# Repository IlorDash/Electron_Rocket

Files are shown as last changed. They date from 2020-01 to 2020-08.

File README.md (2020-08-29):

# Electron_Rocket
Repository for Electron rocket project

Altimeter test - data from altimeter. In .txt files raw data from UART, in excel files altitude graphs. Altitude in centimeters  
BMP_280 Nucleo_L031K6 - code for altimeter  
Camera_Software - rocket-cam project (WIP)  
Model - 3D models of each detail  
Filter_xx - graphs of test of different noise filters  
Real-Rockets_RD1-20-5 - profile of Real Rockets engine for OpenRocket  
Rocket_project - OpenRocket file of my rocket configuration  
rocket_fly_test - data and graph of completed fly test

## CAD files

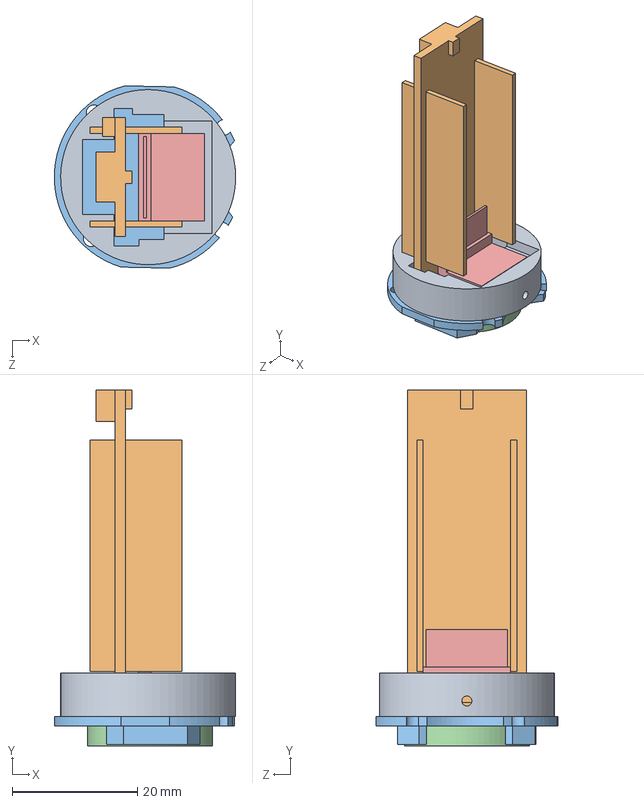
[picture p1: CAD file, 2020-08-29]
Models/Altimeter/Altimeter.SLDASM
29.0 x 56.9 x 29.2 mm
Altimeter_Mount
STM32L031K6
Battery_Mount
Battery_CR2032
BMP_280

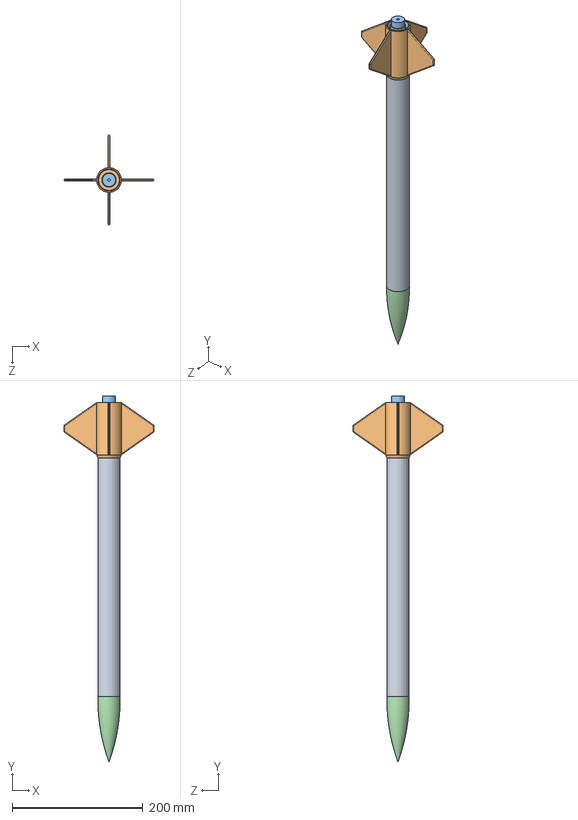
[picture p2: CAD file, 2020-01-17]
Models/Altimeter/Rocket_Assembly.SLDASM
137.9 x 560.0 x 137.9 mm
Body_Tube
Motor_Mount_RD-1-20-5
Motor_RD-1-20-5
Nose_Cone
Altimeter_Mount
STM32L031K6
Battery_Mount
Battery_CR2032
BMP_280
Fins_With_Mount
Parachute_and_rope

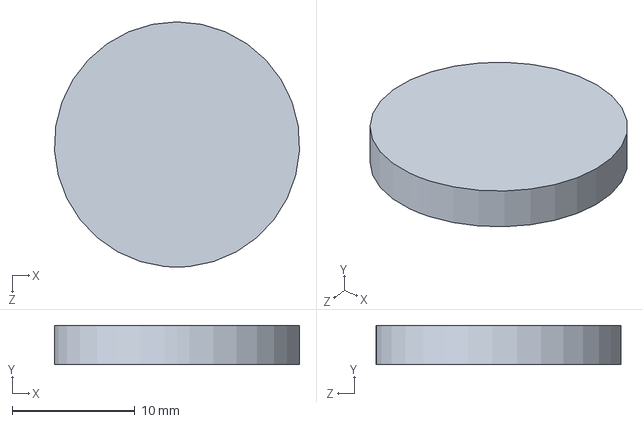
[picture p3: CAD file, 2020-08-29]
Models/Altimeter/Battery_CR2032.SLDPRT
20.0 x 3.20 x 20.0 mm

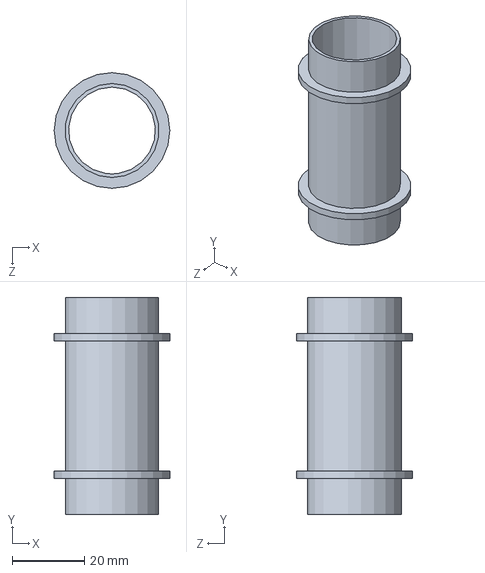
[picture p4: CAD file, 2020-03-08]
Models/Motors/Motor_Mount_RD-1-20(30)-5.SLDPRT
32.0 x 60.0 x 32.0 mm

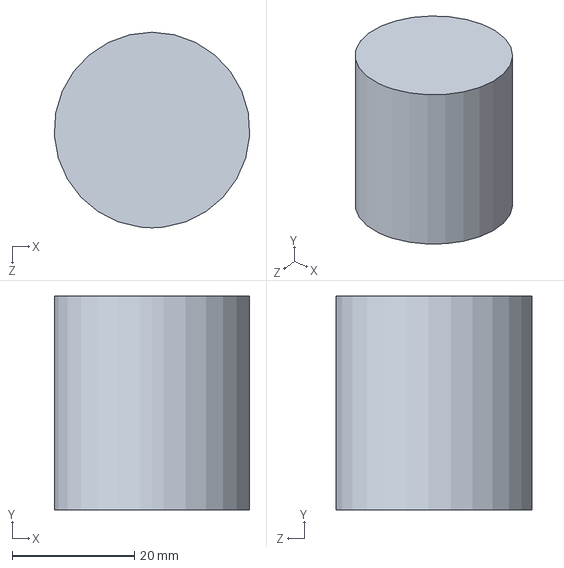
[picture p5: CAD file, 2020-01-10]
Models/Parachute_and_rope.SLDPRT
31.9 x 35.0 x 32.0 mm

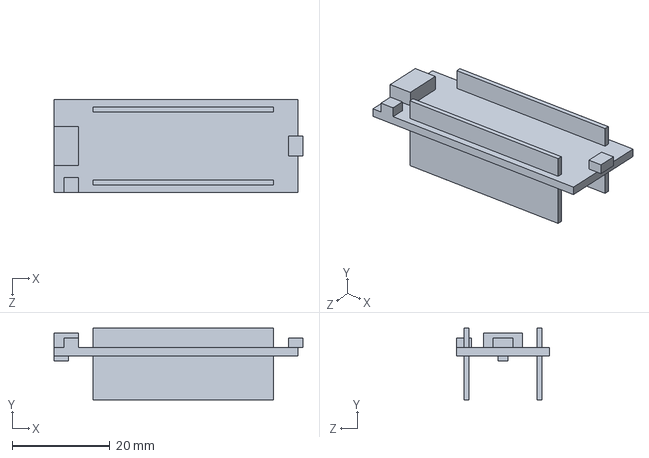
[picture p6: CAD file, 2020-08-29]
Models/Altimeter/STM32L031K6.SLDPRT
51.0 x 14.7 x 19.0 mm

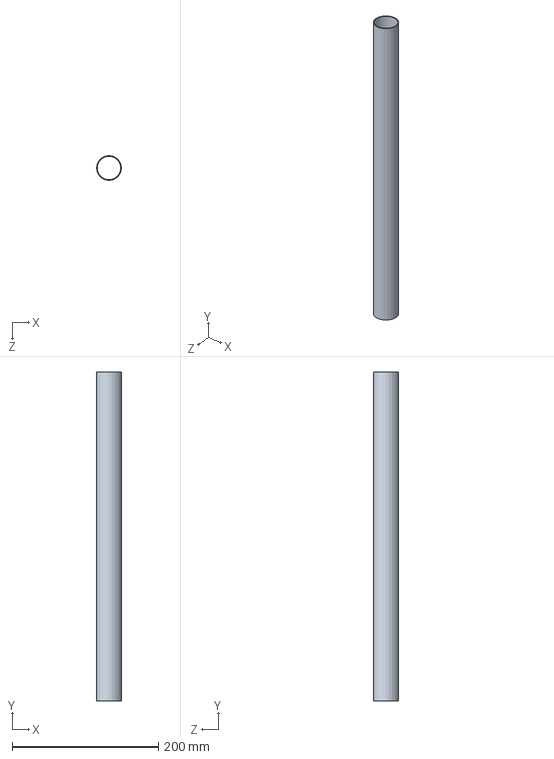
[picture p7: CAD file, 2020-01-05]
Models/Body_Tube.SLDPRT
34.0 x 450.0 x 34.0 mm

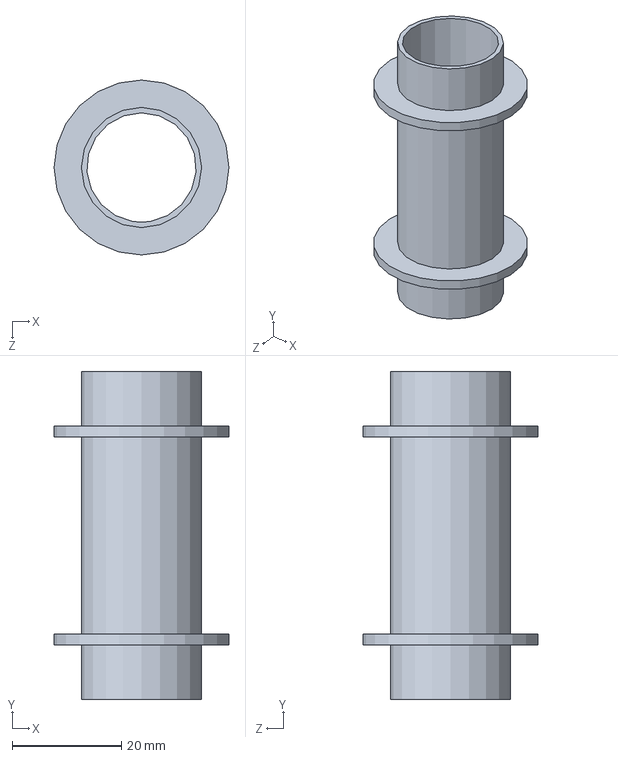
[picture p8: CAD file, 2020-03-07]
Models/Motors/Motor_Mount_RD-1-10-5.SLDPRT
32.0 x 60.0 x 32.0 mm

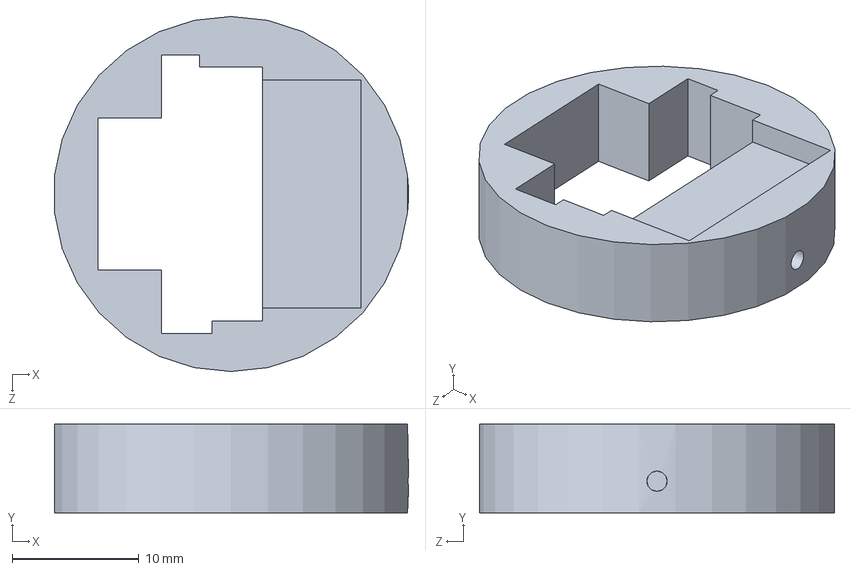
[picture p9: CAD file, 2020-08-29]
Models/Altimeter/Altimeter_Mount.SLDPRT
27.9 x 7.00 x 28.0 mm

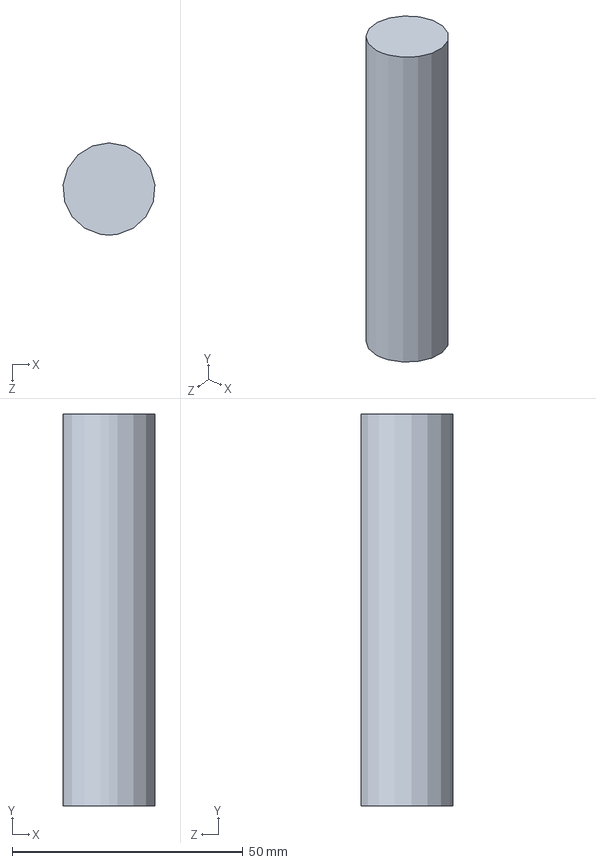
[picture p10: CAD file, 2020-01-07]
Models/Motors/Motor_RD-1-20-5.SLDPRT
19.9 x 85.0 x 20.0 mm

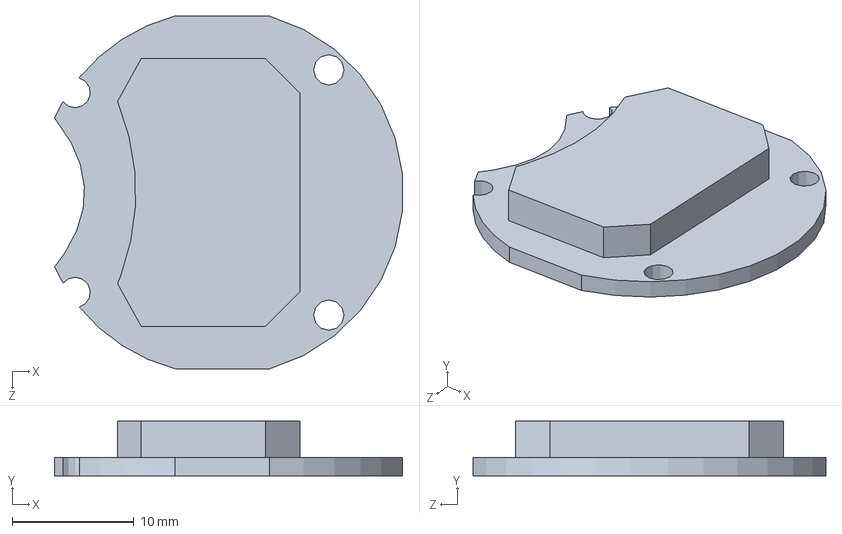
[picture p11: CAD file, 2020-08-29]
Models/Altimeter/Battery_Mount.SLDPRT
28.6 x 4.50 x 29.0 mm

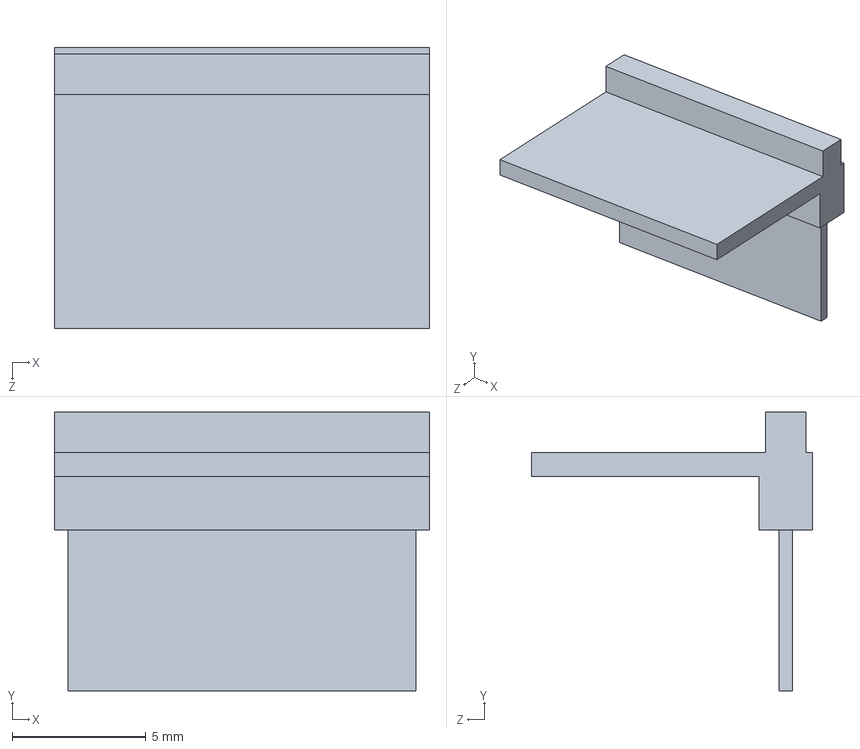
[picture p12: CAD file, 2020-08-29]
Models/Altimeter/BMP_280.SLDPRT
14.0 x 10.4 x 10.5 mm

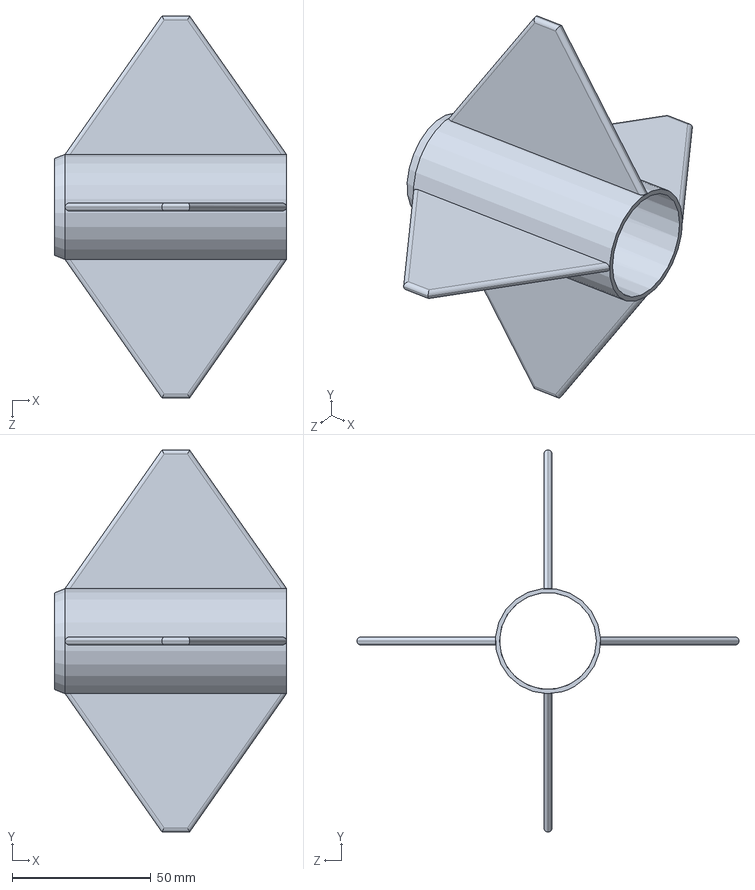
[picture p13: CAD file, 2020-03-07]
Models/Altimeter/Fins_With_Mount.SLDPRT
83.8 x 137.9 x 137.9 mm

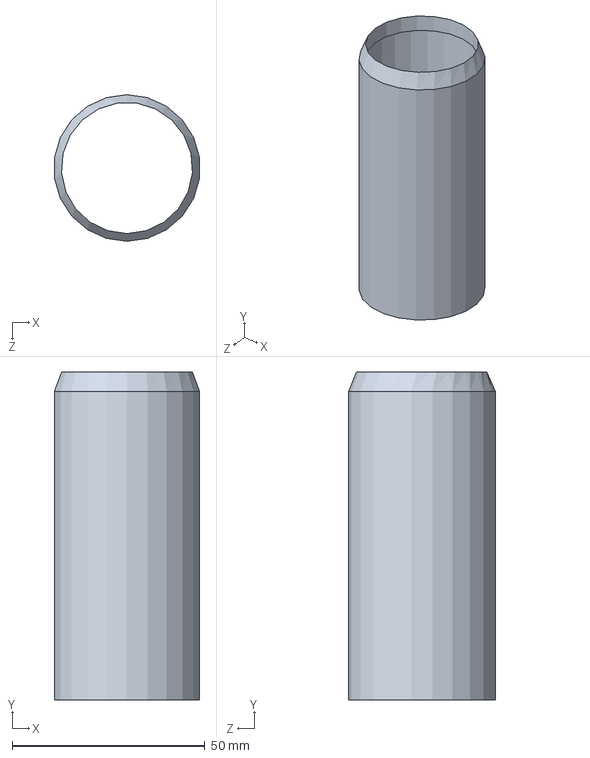
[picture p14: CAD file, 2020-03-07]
Models/Altimeter/Fins_Mount.SLDPRT
37.6 x 85.0 x 38.0 mm

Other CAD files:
Models/Altimeter/Nose_Cone.SLDPRT
Models/Altimeter/Fin.SLDPRT

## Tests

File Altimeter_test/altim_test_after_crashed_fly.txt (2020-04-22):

0	-4
1	-3
2	-2
3	0
4	0
5	2
6	5
7	8
8	8
9	11
10	15
11	17
12	17
13	18
14	20
15	18
16	18
17	17
18	17
19	15
20	15
21	12
22	10
23	9
24	10
25	10
26	10
27	11
28	11
29	13
30	16
31	12
32	14
33	12
34	14
35	16
36	14
37	14
38	14
39	17
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

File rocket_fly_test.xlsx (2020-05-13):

0 | 3 | в метраз | 0.03
1 | 0 |  | 0 | 148.19
2 | 0 |  | 0
3 | 0 |  | 0
4 | 0 |  | 0
5 | 3 |  | 0.03
6 | 2 |  | 0.02
7 | 2 |  | 0.02
8 | 2 |  | 0.02
9 | 2 |  | 0.02
10 | 2 |  | 0.02
11 | 2 |  | 0.02
12 | 5 |  | 0.05
13 | 5 |  | 0.05
14 | 5 |  | 0.05
15 | 4 |  | 0.04
16 | 2 |  | 0.02
17 | 2 |  | 0.02
18 | 2 |  | 0.02
19 | 2 |  | 0.02
20 | 1 |  | 0.01
21 | 1 |  | 0.01
22 | 0 |  | 0
23 | 3 |  | 0.03
24 | 1 |  | 0.01
25 | 1 |  | 0.01
26 | 1 |  | 0.01
27 | 3 |  | 0.03
28 | 3 |  | 0.03
29 | 3 |  | 0.03
30 | 8 |  | 0.08
31 | 8 |  | 0.08
32 | 8 |  | 0.08
33 | 8 |  | 0.08
34 | 8 |  | 0.08
35 | 8 |  | 0.08
36 | 6 |  | 0.06
37 | 6 |  | 0.06
38 | 6 |  | 0.06
39 | 8 |  | 0.08
40 | 6 |  | 0.06
41 | 4 |  | 0.04
42 | 4 |  | 0.04
43 | 4 |  | 0.04
44 | 6 |  | 0.06
45 | 4 |  | 0.04
46 | 8 |  | 0.08
47 | 8 |  | 0.08
48 | 8 |  | 0.08
49 | 9 |  | 0.09
50 | 9 |  | 0.09
51 | 9 |  | 0.09
52 | 9 |  | 0.09
53 | 12 |  | 0.12
54 | 10 |  | 0.1
55 | 10 |  | 0.1
56 | 10 |  | 0.1
57 | 12 |  | 0.12
58 | 12 |  | 0.12
59 | 12 |  | 0.12
60 | 17 |  | 0.17
61 | 17 |  | 0.17
62 | 17 |  | 0.17
63 | 15 |  | 0.15
64 | 15 |  | 0.15
65 | 15 |  | 0.15
66 | 15 |  | 0.15
67 | 15 |  | 0.15
68 | 17 |  | 0.17
69 | 17 |  | 0.17
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

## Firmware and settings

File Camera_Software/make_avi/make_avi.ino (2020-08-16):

/*

  TimeLapseAvi

  ESP32-CAM Video Recorder

  This program records an AVI video on the SD Card of an ESP32-CAM.
  
  by James Zahary July 20, 2019
     jamzah.plc@gmail.com

  https://github.com/jameszah/ESP32-CAM-Video-Recorder
    jameszah/ESP32-CAM-Video-Recorder is licensed under the
    GNU General Public License v3.0

  Acknowlegements:

  1.  https://robotzero.one/time-lapse-esp32-cameras/
      Timelapse programs for ESP32-CAM version that sends snapshots of screen.
  2.  https://github.com/nailbuster/esp8266FTPServer
      ftp server (slightly modifed to get the directory function working)
  3.  https://github.com/ArduCAM/Arduino/tree/master/ArduCAM/examples/mini
      ArduCAM Mini demo (C)2017 LeeWeb: http://www.ArduCAM.com
      I copied the structure of the avi file, some calculations.

  The is Arduino code, with standard setup for ESP32-CAM
    - Board ESP32 Wrover Module
    - Partition Scheme Huge APP (3MB No OTA)
    
  This program records an AVI video on the SD Card of an ESP32-CAM.
  
  It will record realtime video at limited framerates, or timelapses with the full resolution of the ESP32-CAM.
  It is controlled by a web page it serves to stop and start recordings with many parameters, and look through the viewfinder.
  
  You can control framesize (UXGA, VGA, ...), quality, length, and fps to record, and fps to playback later, etc.

  framesize can be UXGA, SVGA, VGA, CIF (default VGA)
  length is length in seconds of the recording 0..3600 (default 1800)
  interval is the milli-seconds between frames (default 200)
  quality is a number 5..50 for the jpeg  - smaller number is higher quality with bigger and more detailed jpeg (default 10)
  repeat is a number of who many of the same recordings should be made (default 100)
  speed is a factor to speed up realtime for a timelapse recording - 1 is realtime (default 1)
  gray is 1 for a grayscale video (default 0 - color)

  These factors have to be within the limit of the SD chip to receive the data.
  For example, using a LEXAR 300x 32GB microSDHC UHS-I, the following works for me:

  UXGA quality 10,  2 fps (or interval of 500ms)
  SVGA quality 10,  5 fps (200ms)
  VGA  quality 10, 10 fps (100ms)
  CIG  quality 10, 20 fps (50ms)

  If you increase fps, you might have to reduce quality or framesize to keep it from dropping frames as it writes all the data to the SD chip.

  Also, other SD chips will be faster or slower.  I was using a SanDisk 16GB microSDHC "Up to 653X" - which was slower and more unpredictable than the LEXAR ???

  Search for "zzz" to find places to modify the code for:
    1.  Your wifi name and password
    2.  Your preferred ip address (with default gateway, etc)
    3.  Your Timezone for use in filenames
    4.  Defaults for framesize, quality, ... and if the recording should start on reboot of the ESP32 without receiving a command
  
*/



#include "esp_camera.h"

// MicroSD
#include "driver/sdmmc_host.h"
#include "driver/sdmmc_defs.h"
#include "sdmmc_cmd.h"
#include "SD_MMC.h"
#include "esp_vfs_fat.h"

//nrf24
#include  <SPI.h>
#include "nRF24L01.h"
#include "RF24.h"

//vars for nrf24
char msg[6] = "hello";
bool radioNeedSetup = true;
RF24 radio(2, 15, 14, 12, 13);
const uint64_t _pipe = 0xE8E8F0F0E1LL;

void radioSetup(){
  radio.begin();
  radio.setChannel(120);
  radio.setPayloadSize(7);
  radio.openWritingPipe(_pipe);
  radio.setDataRate(RF24_250KBPS);
  radio.setPALevel(RF24_PA_MAX);
  radio.powerUp(); //начать работу
  radio.stopListening();  //не слушаем радиоэфир, мы передатчик
  radio.printDetails(); 
}

// my variables
#define LED_PIN 3
#define BUTTON_PIN 13

unsigned long lastFlash = 0;
bool record = false;

long current_millis;
long last_capture_millis = 0;
static esp_err_t cam_err;
static esp_err_t card_err;
char strftime_buf[64];
int file_number = 0;
bool internet_connected = false;
struct tm timeinfo;
time_t now;

char *filename ;
char *stream ;
int newfile = 0;
int frames_so_far = 0;
FILE *myfile;
long bp;
long ap;
long bw;
long aw;
long totalp;
long totalw;
float avgp;
float avgw;
int overtime_count = 0;

// CAMERA_MODEL_AI_THINKER
#define PWDN_GPIO_NUM     32
#define RESET_GPIO_NUM    -1
#define XCLK_GPIO_NUM      0
#define SIOD_GPIO_NUM     26
#define SIOC_GPIO_NUM     27
#define Y9_GPIO_NUM       35
#define Y8_GPIO_NUM       34
#define Y7_GPIO_NUM       39
#define Y6_GPIO_NUM       36
#define Y5_GPIO_NUM       21
#define Y4_GPIO_NUM       19
#define Y3_GPIO_NUM       18
#define Y2_GPIO_NUM        5
#define VSYNC_GPIO_NUM    25
#define HREF_GPIO_NUM     23
#define PCLK_GPIO_NUM     22


// GLOBALS
#define BUFFSIZE 512



// these are just declarations -- look below to edit defaults 

int capture_interval = 200; // microseconds between captures
int total_frames = 300;     // default updated below
int recording = 1;          // default start recording on reboot
int framesize = 6;          // vga
int repeat = 100;           // capture 100 videos
int quality = 10;
int xspeed = 1;
int xlength = 3;
int gray = 0;

int delay_between_captures = 0;

#define AVIOFFSET 240 // AVI main header length

unsigned long movi_size = 0;
unsigned long jpeg_size = 0;
unsigned long idx_offset = 0;

uint8_t zero_buf[4] = {0x00, 0x00, 0x00, 0x00};
uint8_t   dc_buf[4] = {0x30, 0x30, 0x64, 0x63};    // "00dc"
uint8_t avi1_buf[4] = {0x41, 0x56, 0x49, 0x31};    // "AVI1"
uint8_t idx1_buf[4] = {0x69, 0x64, 0x78, 0x31};    // "idx1"

uint8_t  vga_w[2] = {0x80, 0x02}; // 640
uint8_t  vga_h[2] = {0xE0, 0x01}; // 480
uint8_t  cif_w[2] = {0x90, 0x01}; // 400
uint8_t  cif_h[2] = {0x28, 0x01}; // 296
uint8_t svga_w[2] = {0x20, 0x03}; //
uint8_t svga_h[2] = {0x58, 0x02}; //
uint8_t uxga_w[2] = {0x40, 0x06}; // 1600
uint8_t uxga_h[2] = {0xB0, 0x04}; // 1200


const int avi_header[AVIOFFSET] PROGMEM = {
  0x52, 0x49, 0x46, 0x46, 0xD8, 0x01, 0x0E, 0x00, 0x41, 0x56, 0x49, 0x20, 0x4C, 0x49, 0x53, 0x54,
  0xD0, 0x00, 0x00, 0x00, 0x68, 0x64, 0x72, 0x6C, 0x61, 0x76, 0x69, 0x68, 0x38, 0x00, 0x00, 0x00,
  0xA0, 0x86, 0x01, 0x00, 0x80, 0x66, 0x01, 0x00, 0x00, 0x00, 0x00, 0x00, 0x10, 0x00, 0x00, 0x00,
  0x64, 0x00, 0x00, 0x00, 0x00, 0x00, 0x00, 0x00, 0x01, 0x00, 0x00, 0x00, 0x00, 0x00, 0x00, 0x00,
  0x80, 0x02, 0x00, 0x00, 0xe0, 0x01, 0x00, 0x00, 0x00, 0x00, 0x00, 0x00, 0x00, 0x00, 0x00, 0x00,
  0x00, 0x00, 0x00, 0x00, 0x00, 0x00, 0x00, 0x00, 0x4C, 0x49, 0x53, 0x54, 0x84, 0x00, 0x00, 0x00,
  0x73, 0x74, 0x72, 0x6C, 0x73, 0x74, 0x72, 0x68, 0x30, 0x00, 0x00, 0x00, 0x76, 0x69, 0x64, 0x73,
  0x4D, 0x4A, 0x50, 0x47, 0x00, 0x00, 0x00, 0x00, 0x00, 0x00, 0x00, 0x00, 0x00, 0x00, 0x00, 0x00,
  0x01, 0x00, 0x00, 0x00, 0x01, 0x00, 0x00, 0x00, 0x00, 0x00, 0x00, 0x00, 0x0A, 0x00, 0x00, 0x00,
  0x00, 0x00, 0x00, 0x00, 0x00, 0x00, 0x00, 0x00, 0x00, 0x00, 0x00, 0x00, 0x73, 0x74, 0x72, 0x66,
  0x28, 0x00, 0x00, 0x00, 0x28, 0x00, 0x00, 0x00, 0x80, 0x02, 0x00, 0x00, 0xe0, 0x01, 0x00, 0x00,
  0x01, 0x00, 0x18, 0x00, 0x4D, 0x4A, 0x50, 0x47, 0x00, 0x84, 0x03, 0x00, 0x00, 0x00, 0x00, 0x00,
  0x00, 0x00, 0x00, 0x00, 0x00, 0x00, 0x00, 0x00, 0x00, 0x00, 0x00, 0x00, 0x49, 0x4E, 0x46, 0x4F,
  0x10, 0x00, 0x00, 0x00, 0x6A, 0x61, 0x6D, 0x65, 0x73, 0x7A, 0x61, 0x68, 0x61, 0x72, 0x79, 0x67,
  0x6D, 0x61, 0x69, 0x6C, 0x4C, 0x49, 0x53, 0x54, 0x00, 0x01, 0x0E, 0x00, 0x6D, 0x6F, 0x76, 0x69,
};


//
// Writes an uint32_t in Big Endian at current file position
//
static void inline print_quartet(unsigned long i, FILE * fd)
{
  uint8_t x[1];

  x[0] = i % 0x100;
  size_t i1_err = fwrite(x , 1, 1, fd);
  i = i >> 8;  x[0] = i % 0x100;
  size_t i2_err = fwrite(x , 1, 1, fd);
  i = i >> 8;  x[0] = i % 0x100;
  size_t i3_err = fwrite(x , 1, 1, fd);
  i = i >> 8;  x[0] = i % 0x100;
  size_t i4_err = fwrite(x , 1, 1, fd);
}

char the_page[3000];

#include "soc/soc.h"
#include "soc/rtc_cntl_reg.h"


void setup() {


  Serial.begin(115200);

  Serial.setDebugOutput(true);
  


  pinMode(33, OUTPUT);    // little red led on back of chip
  //pinMode (LED_BUILTIN, OUTPUT); // flash light
  pinMode(LED_PIN, OUTPUT);
  pinMode(BUTTON_PIN, INPUT);

  digitalWrite(33, LOW);           // turn on the red LED on the back of chip

  camera_config_t config;
  config.ledc_channel = LEDC_CHANNEL_0;
  config.ledc_timer = LEDC_TIMER_0;
  config.pin_d0 = Y2_GPIO_NUM;
  config.pin_d1 = Y3_GPIO_NUM;
  config.pin_d2 = Y4_GPIO_NUM;
  config.pin_d3 = Y5_GPIO_NUM;
  config.pin_d4 = Y6_GPIO_NUM;
  config.pin_d5 = Y7_GPIO_NUM;
  config.pin_d6 = Y8_GPIO_NUM;
  config.pin_d7 = Y9_GPIO_NUM;
  config.pin_xclk = XCLK_GPIO_NUM;
  config.pin_pclk = PCLK_GPIO_NUM;
  config.pin_vsync = VSYNC_GPIO_NUM;
  config.pin_href = HREF_GPIO_NUM;
  config.pin_sscb_sda = SIOD_GPIO_NUM;
  config.pin_sscb_scl = SIOC_GPIO_NUM;
  config.pin_pwdn = PWDN_GPIO_NUM;
  config.pin_reset = RESET_GPIO_NUM;
  config.xclk_freq_hz = 20000000;
  config.pixel_format = PIXFORMAT_JPEG;

  //init with high specs to pre-allocate larger buffers
  if (psramFound()) {
    config.frame_size = FRAMESIZE_UXGA;
    config.jpeg_quality = 1;
    config.fb_count = 2;
  } else {
    config.frame_size = FRAMESIZE_SVGA;         // svga 12 fails due to jpg 60000
    config.jpeg_quality = 12;
    config.fb_count = 1;
  }

  // camera init
  
  cam_err = esp_camera_init(&config);
  if (cam_err != ESP_OK) {
    Serial.printf("Camera init failed with error 0x%x", cam_err);
    major_fail();
    return;
  }

  // SD camera init
  card_err = init_sdcard();
  SD_MMC.begin("/sdcard", true);
  if (card_err != ESP_OK) {
    Serial.printf("SD Card init failed with error 0x%x", card_err);
    major_fail();
    return;
  }

  // 200 ms x 150 frames = 30 seconds     is 3 MB indoors
  // 200 ms x 300 frames = 1 minute       is about 6MD indoor
  // 20 ms x 3000 frames = 10 minute      is 60 MB indoor
  // burst 1000 frames gives 8 fps rather than 5, so 2 minutues 20 MB indoor

  digitalWrite(33, HIGH);


  //
  //  startup defaults  -- EDIT HERE 
  //  zzz

  sensor_t * s = esp_camera_sensor_get();
  s->set_framesize(s, FRAMESIZE_VGA);
  s->set_quality(s, 10);
  do_fb();                  // do a couple captures to make sure camera has new config
  do_fb();

  framesize = 6;            // vga
  repeat = 0;             // video + 1
  xspeed = 1;               // playback at 1 x realtime
  gray = 0;                 // not gray

  quality = 50;             // quality 10 - pretty good.  Goes from 0..63, but 0-5 sometimes fails on bright scenery (jpg too big for ESP32CAM system)
  capture_interval = 2;   //  milli-secconds per frame
  delay_between_captures = 45;

  total_frames = 100;       // total_frames x capture_interval = record_timea
  
  xlength = total_frames * (capture_interval + delay_between_captures); // in ms

  newfile = 0;    // no file is open  // don't fiddle with this!
  recording = 1;  // start recording on reboot without sending a command

}

//
// if we have no camera, or sd card, then flash rear led on and off to warn the human SOS - SOS
//
void major_fail() {
  while (1) {
    digitalWrite(33, LOW);
    delay(100);
    digitalWrite(33, HIGH);
    delay(100);

    digitalWrite(33, LOW);
    delay(100);
    digitalWrite(33, HIGH);
    delay(100);

    digitalWrite(33, LOW);
    delay(100);
    digitalWrite(33, HIGH);
    //delay(100);

    delay(1000);

    digitalWrite(33, LOW);
    delay(500);
    digitalWrite(33, HIGH);
    delay(500);

    digitalWrite(33, LOW);
    delay(500);
    digitalWrite(33, HIGH);
    delay(500);

    digitalWrite(33, LOW);
    delay(500);
    digitalWrite(33, HIGH);
    //delay(500);

    delay(1000);
  }
}

static esp_err_t init_sdcard()
{

  esp_err_t ret = ESP_FAIL;
  sdmmc_host_t host = SDMMC_HOST_DEFAULT();
  sdmmc_slot_config_t slot_config = SDMMC_SLOT_CONFIG_DEFAULT();
  esp_vfs_fat_sdmmc_mount_config_t mount_config = {
    .format_if_mount_failed = false,
    .max_files = 10,
  };
  sdmmc_card_t *card;

  Serial.println("Mounting SD card...");
  ret = esp_vfs_fat_sdmmc_mount("/sdcard", &host, &slot_config, &mount_config, &card);

  if (ret == ESP_OK) {
    Serial.println("SD card mount successfully!");
  }  else  {
    Serial.printf("Failed to mount SD card VFAT filesystem. Error: %s", esp_err_to_name(ret));
    major_fail();
  }

  Serial.print("SD_MMC Begin: "); Serial.println(SD_MMC.begin());   // required by ftp system ??
}

//////////////////////////////////////////////////////////////
// save photo stuff not currently used

static esp_err_t save_photo_numbered()
{
  file_number++;
  Serial.print("Taking picture: ");
  Serial.print(file_number);
  camera_fb_t *fb = esp_camera_fb_get();

  char *filename = (char*)malloc(21 + sizeof(int));
  sprintf(filename, "/sdcard/capture_%d.jpg", file_number);

  Serial.println(filename);
  FILE *file = fopen(filename, "w");
  if (file != NULL)  {
    size_t err = fwrite(fb->buf, 1, fb->len, file);
    Serial.printf("File saved: %s\n", filename);
  }  else  {
    Serial.println("Could not open file");
  }
  fclose(file);
  esp_camera_fb_return(fb);
  free(filename);
}



static esp_err_t save_photo_dated()
{
  Serial.println("Taking a picture...");
  camera_fb_t *fb = esp_camera_fb_get();

  time(&now);
  localtime_r(&now, &timeinfo);
  strftime(strftime_buf, sizeof(strftime_buf), "%F__%H%M%S", &timeinfo);

  char fname[100];

  if (framesize == 6) {
    sprintf(fname, "/sdcard/%s_vga_%d.jpg", strftime_buf, quality);
  } else if (framesize == 7) {
    sprintf(fname, "/sdcard/%s_svga_%d.jpg", strftime_buf, quality);
  } else if (framesize == 10) {
    sprintf(fname, "/sdcard/%s_uxga_%d.jpg", strftime_buf, quality);
  } else  if (framesize == 5) {
    sprintf(fname, "/sdcard/%s_cif_%d.jpg", strftime_buf, quality);
  } else {
    Serial.println("Wrong framesize");
    sprintf(fname, "/sdcard/%s_xxx_%d.jpg", strftime_buf, quality);
  }

  FILE *file = fopen(fname, "w");
  if (file != NULL)  {
    size_t err = fwrite(fb->buf, 1, fb->len, file);
    Serial.printf("File saved: %s\n", fname);

  }  else  {
    Serial.println("Could not open file");
  }
  fclose(file);
  esp_camera_fb_return(fb);

}

void save_photo()
{
  if (timeinfo.tm_year < (2016 - 1900) || internet_connected == false) { // if no internet or time not set
    save_photo_numbered(); // filenames in numbered order
  } else {
    save_photo_dated(); // filenames with date and time
  }
}



//~~~~~~~~~~~~~~~~~~~~~~~~~~~~~~~~~~~~~~~~~~~~~~~~~~~~~~~~~~~~~~~~~~~~~~~~~~~~~~~~~
//
// Make the avi move in 4 pieces
//
// make_avi() called in every loop, which calls below, depending on conditions
//   start_avi() - open the file and write headers
//   another_pic_avi() - write one more frame of movie
//   end_avi() - write the final parameters and close the file

// global variable used by these pieces

char str[20];
uint16_t n;
uint8_t buf[BUFFSIZE];

static int i = 0;
uint8_t temp = 0, temp_last = 0;
unsigned long fileposition = 0;
uint16_t frame_cnt = 0;
uint16_t remnant = 0;
uint32_t length = 0;
uint32_t startms;
uint32_t elapsedms;
uint32_t uVideoLen = 0;
bool is_header = false;
long bigdelta = 0;

camera_fb_t * fb = NULL;

FILE *avifile = NULL;
FILE *idxfile = NULL;

void make_avi( ) {

  // we are recording, but no file is open

  if (newfile == 0 && recording == 1) {                                     // open the file

    //save_photo_dated();

    start_avi();

    digitalWrite(33, HIGH);
    newfile = 1;
    totalp = 0;
    totalw = 0;
    frame_cnt = 0;
    frames_so_far = 0;

  } else {

    // we have a file open, but not recording

    if (newfile == 1 && recording == 0) {                                  // got command to close file
      digitalWrite(33, LOW);

      end_avi();

      Serial.println("Done capture due to command");

      frames_so_far = total_frames;

      newfile = 0;    // file is closed
      recording = 0;  // DO NOT start another recording

    } else {

      if (newfile == 1 && recording == 1) {                            // regular recording

        if (frames_so_far == total_frames)  {                                // we are done the recording

          Serial.println("Done capture for total frames!");

          digitalWrite(33, LOW);                                                       // close the file
          end_avi();

          frames_so_far = 0;
          newfile = 0;          // file is closed

          if (repeat > 0) {
            recording = 1;        // start another recording
            repeat = repeat - 1;
          } else {
            recording = 0;
          }
          
        } else if ((millis() - startms) > xlength) {

          Serial.println (" "); Serial.println("Done capture for time");
          Serial.print("Time Elapsed: "); Serial.print(millis() - startms); Serial.print(" Frames: "); Serial.println(frame_cnt);
          Serial.print("Config:       "); Serial.print(total_frames * capture_interval ) ; Serial.print(" (");
          Serial.print(total_frames); Serial.print(" x "); Serial.print(capture_interval);  Serial.println(")");

          digitalWrite(33, LOW);                                                       // close the file

          end_avi();

          frames_so_far = 0;
          newfile = 0;          // file is closed
          if (repeat > 0) {
            recording = 1;        // start another recording
            repeat = repeat - 1;
          } else {
            recording = 0;
          }

        } else  {                                                            // regular

          /*current_millis = millis();

          if (current_millis - last_capture_millis > capture_interval) {   */                    // Take another picture - fixed interval

            //if ((current_millis - startms) > (frame_cnt * capture_interval)) {                   // Take another picture - with catch up

            //last_capture_millis = millis();

            frames_so_far = frames_so_far + 1;
            frame_cnt++;

            another_pic_avi();
            
          //}
        }
      }
    }
  }
}
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
void loop()
{
  if (((digitalRead(BUTTON_PIN) == HIGH) || (record == true)) && (recording == 1))
    {
        if ((millis() - time_after_last_capture) >= delay_between_captures)             //make_avi check
        {
          make_avi();
          time_after_last_capture = millis();
        }
        
        
        record = true;
        
        if (millis() - lastFlash >= 1000)
        {
          lastFlash = millis();
          digitalWrite(LED_PIN, HIGH); //flash light
        } else if(millis() - lastFlash >= 1000)
        {
          digitalWrite(LED_PIN, LOW); //off light
          lastFlash = millis();
        }       
    }
    if(recording == 0){
      if(radioNeedSetup){
        radioSetup();
        radioNeedSetup = false;
      }
      Serial.print("Sending ");
      Serial.println(msg);
      radio.write(msg, 6);
      delay(10);
    }
    
}

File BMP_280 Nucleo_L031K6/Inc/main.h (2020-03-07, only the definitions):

#define TMS_Pin GPIO_PIN_13
#define TMS_GPIO_Port GPIOA
#define TCK_Pin GPIO_PIN_14
#define TCK_GPIO_Port GPIOA
#define LD3_Pin GPIO_PIN_3
#define LD3_GPIO_Port GPIOB
#define VCP_TX_Pin GPIO_PIN_6
#define VCP_TX_GPIO_Port GPIOB
#define VCP_RX_Pin GPIO_PIN_7
#define VCP_RX_GPIO_Port GPIOB

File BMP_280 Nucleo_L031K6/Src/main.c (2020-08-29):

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

/* Includes ------------------------------------------------------------------*/
#include "main.h"

/* USER CODE BEGIN Includes */
#include "bmp280.h"
/* USER CODE END Includes */

/* USER CODE BEGIN PTD */
#define MEASURMENTS_NUM 50
#define NUM_OF_FLASH_CELLS 4096
#include <string.h>
#include <stdio.h>
/* USER CODE END PTD */

I2C_HandleTypeDef hi2c1;

UART_HandleTypeDef huart2;

BMP280_HandleTypedef bmp280;

/* USER CODE BEGIN PV */
float pressure, temperature, humidity;

uint32_t data_to_flash;
uint8_t data_to_uart[128];
uint16_t size_to_uart;
float altitude_0 = 0;
float altitude_above_ground = 0;
float altitude_above_ground_prev = 0;
float altitude_t = 0;
float altitude_current = 0;
float altitude_to_flash = 0;
uint8_t flash_step = 4; // 4 bytes for measurment

char *status = "";
/* USER CODE END PV */

void SystemClock_Config(void);
static void MX_GPIO_Init(void);
static void MX_USART2_UART_Init(void);
static void MX_I2C1_Init(void);
/* USER CODE BEGIN PFP */

bool SaveFlashData(uint32_t dest, uint32_t *pSrc, uint16_t size) {
	while (HAL_FLASH_Unlock() != HAL_OK) {
	}

	uint32_t *pDest = (uint32_t *)dest;
	uint32_t *pDestEnd = pDest + size;
	uint32_t pageToBeErase = (uint32_t)pDest & ~(FLASH_PAGE_SIZE - 1);
	while (pDest < pDestEnd) {
		if (FLASH_WaitForLastOperation(FLASH_TIMEOUT_VALUE * 2) != HAL_OK) {
			break;
		}

		if (pageToBeErase == (uint32_t)pDest) {
			int cmpSize = (pDestEnd - pDest) * sizeof(uint32_t);
			if (cmpSize > FLASH_PAGE_SIZE) {
				cmpSize = FLASH_PAGE_SIZE;
			}
			bool pageIsEqual = memcmp(pDest, pSrc, cmpSize) == 0;
			if (pageIsEqual) {
				pDest += FLASH_PAGE_SIZE / sizeof(uint32_t);
				pSrc += FLASH_PAGE_SIZE / sizeof(uint32_t);
				pageToBeErase = (uint32_t)pDest & ~(FLASH_PAGE_SIZE - 1);
				continue;
			} else {
				SET_BIT(FLASH->PECR, FLASH_PECR_ERASE); /* Set the ERASE bit */
				SET_BIT(FLASH->PECR, FLASH_PECR_PROG);	/* Set PROG bit */

				*(__IO uint32_t *)(uint32_t)pageToBeErase = 0x00000000; /* Write 00000000h to the first word of the program page to erase */
				if (FLASH_WaitForLastOperation(FLASH_TIMEOUT_VALUE * 2) != HAL_OK) {
					break;
				}
				CLEAR_BIT(FLASH->PECR, FLASH_PECR_PROG);
				CLEAR_BIT(FLASH->PECR, FLASH_PECR_ERASE);
				pageToBeErase = ((uint32_t)pDest & ~(FLASH_PAGE_SIZE - 1)) + FLASH_PAGE_SIZE;
			}
		}
		*(__IO uint32_t *)pDest = *pSrc;
		pDest++;
		pSrc++;
	}

	// timeout = SysTickCount;
	/*while (HAL_FLASH_Lock() != HAL_OK) {
		if (PeriodInRange(timeout, SYSTICK_mS(2))) {
			return false;
		}
	}*/
	return true;
}

/* USER CODE END PFP */

/**
 * @brief  The application entry point.
 * @retval int
 */
int main(void) {
	/* MCU Configuration--------------------------------------------------------*/

	/* Reset of all peripherals, Initializes the Flash interface and the Systick. */
	HAL_Init();

	/* Configure the system clock */
	SystemClock_Config();

	/* Initialize all configured peripherals */
	MX_GPIO_Init();
	MX_USART2_UART_Init();
	MX_I2C1_Init();
	/* USER CODE BEGIN 2 */
	int i = 0;
	GPIO_PinState currentButtonState;
	while (i < 50) {
		currentButtonState = HAL_GPIO_ReadPin(GPIOA, GPIO_PIN_4);
		if (currentButtonState == GPIO_PIN_RESET) {
			break;
		}
		HAL_Delay(100);
		i++;
	}

	// MAIN CONDITION
	if (currentButtonState == GPIO_PIN_RESET) {
		status = "measurment";
		bmp280_init_user_params(&bmp280.params);
		bmp280.addr = BMP280_I2C_ADDRESS_0;
		bmp280.i2c = &hi2c1;

		while (!bmp280_init(&bmp280, &bmp280.params)) {
			HAL_Delay(2000);
		}
		HAL_GPIO_WritePin(LD3_GPIO_Port, LD3_Pin, GPIO_PIN_SET);
		HAL_Delay(1000);
		HAL_GPIO_WritePin(LD3_GPIO_Port, LD3_Pin, GPIO_PIN_RESET);
		HAL_Delay(500);
		HAL_GPIO_WritePin(LD3_GPIO_Port, LD3_Pin, GPIO_PIN_SET);
		HAL_Delay(1000);
		HAL_GPIO_WritePin(LD3_GPIO_Port, LD3_Pin, GPIO_PIN_RESET);
		// bool bme280p = bmp280.id == BME280_CHIP_ID;

		// findind null altitude
		HAL_Delay(100);
		i = 0;
		while (i < MEASURMENTS_NUM) {
			while (!bmp280_read_float(&bmp280, &temperature, &pressure, &humidity)) {
				HAL_Delay(2000);
			}
			altitude_t += calculate_altitude(temperature, pressure);
			i++;
			HAL_Delay(100);
		}
		altitude_0 = altitude_t / MEASURMENTS_NUM;

		i = 0;
		int j = 1;
		HAL_GPIO_WritePin(LD3_GPIO_Port, LD3_Pin, GPIO_PIN_SET);
		HAL_Delay(1000);
		HAL_GPIO_WritePin(LD3_GPIO_Port, LD3_Pin, GPIO_PIN_RESET);
		HAL_Delay(500);
		HAL_GPIO_WritePin(LD3_GPIO_Port, LD3_Pin, GPIO_PIN_SET);
		HAL_Delay(1000);
		HAL_GPIO_WritePin(LD3_GPIO_Port, LD3_Pin, GPIO_PIN_RESET);


		while (i < NUM_OF_FLASH_CELLS) {            //main measurments to FLASH
			HAL_Delay(99);
			while (!bmp280_read_float(&bmp280, &temperature, &pressure, &humidity)) {
				HAL_Delay(2000);
			}                                                                                   //calculating altitude
			altitude_above_ground = calculate_altitude(temperature, pressure);
			int16_t val = (int)((altitude_above_ground - altitude_0) * 100);

			bool isOddIter = (i & 0x0001) != 0;                                                 
			if (isOddIter) {
				data_to_flash = data_to_flash + ((val << 16) & 0xFFFF0000);
				SaveFlashData(0x08006000 + ((i - j) * sizeof(uint32_t)), &data_to_flash, 1);
				j++;                                                                                //save altitude data to flash
				HAL_Delay(2);
			} else {
				data_to_flash = val & 0x0000FFFF;
			}
			i++;
		}
	} else {                                          
		status = "transmiting to UART";
		HAL_GPIO_WritePin(LD3_GPIO_Port, LD3_Pin, GPIO_PIN_SET);
		i = 0;
		while (i < NUM_OF_FLASH_CELLS) {
			data_to_flash = *(__IO uint32_t *)(0x08006000 + (i * sizeof(uint32_t)));
			int16_t val0 = (int16_t)(data_to_flash & 0x0000FFFF);
			int16_t val1 = (int16_t)((data_to_flash >> 16) & 0x0000FFFF);

			size_to_uart = sprintf((char *)data_to_uart, "%05d  %06d  %06d \n", i, val0, val1);
			HAL_UART_Transmit(&huart2, data_to_uart, size_to_uart, 100);
			HAL_Delay(100);
			i++;
		}
	}

	/* USER CODE END 2 */

	/* Infinite loop */
	/* USER CODE BEGIN WHILE */
	while (1) {                                                               
		HAL_GPIO_WritePin(LD3_GPIO_Port, LD3_Pin, GPIO_PIN_SET);
		HAL_Delay(500);                                                           //after transmit or measurment start blink
		HAL_GPIO_WritePin(LD3_GPIO_Port, LD3_Pin, GPIO_PIN_RESET);
		HAL_Delay(1000);
		/* USER CODE END WHILE */

		/* USER CODE BEGIN 3 */
	}
	/* USER CODE END 3 */
}

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


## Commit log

2020-01-05 added first files
    [Body_Tube.SLDPRT, Motor_Mount_RD-1-20-5.SLDPRT, Motor_RD-1-20-5.SLDPRT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]
2020-01-07 finished shape of rocket (nose cone, fins, fins mount), made model of rocket. TODO: model of altimeter
    [Altimeter_Mount.SLDPRT, Fin.SLDPRT, Fins_Mount.SLDPRT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]
2020-01-10 finished rocket design development
    [Altimeter.SLDASM, Altimeter_Mount.SLDPRT, BMP_280.SLDPRT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]
2020-01-10 rewrited density of plastic parts and added parachute and rope mass object in model
    [Altimeter.SLDASM, Altimeter_Mount.SLDPRT, Fin.SLDPRT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]
2020-01-12 fixed sizes of altimeter mount in view printed detail
    [Altimeter_Mount.SLDPRT]
2020-01-17 fixed sizes of altimeter and nose cone, changed thickness of nose cone from 2mm to 2.5mm, it gaves + 3.8 gramm, changed mount altimeter to nose cone to one self-tapping screw on the side
    [Altimeter.SLDASM, Altimeter_Mount.SLDPRT, Nose_Cone.SLDPRT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]
2020-03-07 fixed sizes of motor mounts and nose cone according to real sizes of printed models
    [Fins_Mount.SLDPRT, Fins_With_Mount.SLDPRT, Motor_Mount_RD-1-10-5.SLDPRT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]
2020-03-07 added BMP280 filters plots
    [Filter_16.xlsx, Filter_8.xlsx, Filter_OFF.xlsx]
2020-03-07 added plot of electronic specifications
    [Лист Microsoft Excel.xlsx, Электроника.xlsx]
2020-03-07 added handler of measurments or transmit to UART, calculating altitude to Flash, TODO: fix safe to flash function
    [BMP_280 Nucleo_L031K6.ioc, main.c]
2020-03-08 added LED blinking when its meausurming and find problems with decreasing float from float and SaveFlashData
    [main.c]
2020-03-08 fixed density of motor mount concerning of mass of printed details
    [Motor_Mount_RD-1-20(30)-5.SLDPRT]
2020-03-08 fixed bugs with float decreasing, flash safe and uart
    [main.c]
2020-03-08 changed output format to UART, output unit to centimeter
2020-03-09 changed output UART format to work with excel
2020-03-11 changed light detection in writing mode: if BMP280 is working, then light blinks, when ground level is calculated, then light blinks once more
2020-03-13 fixed bugs with half memory recording and odd counter, changed filter of BMP280 data to 16x
    [bmp280.c, main.c]
2020-03-18 added data of all altimeter test
    [ROcket3.xlsx, Rocket4.xlsx, Rocket5.xlsx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]
2020-04-07 added plot of rocket flight test witn non-working engines, when rocket falls down and stabilizer broke
    [rocket_flight_fall_test.xlsx]
2020-04-22 checked altimeter after crashed fly, added plots of altimeter work
    [altim_stable_test_after_crashed_fly.xlsx, altim_test_after_crashed_fly.xlsx, rocket_flight_fall_test.xlsx]
2020-05-13 added data of altimeter fly test
    [rocket_fly_altimeter.xlsx]
2020-07-23 added control of start recording via button and display if recording via LED
2020-07-24 added code for nrf24 client and server with 18dBm transmit power and 250kbps data rate
    -server only receive
    -client only transmit
2020-07-29 added params for nice camera recordin (8 fps on 128MB fast sd card)
2020-07-29 added code for ESP32 Cam with nrf24 and radio library TODO: check program
2020-08-11 added grid for thrust curves and example of grid for RD1-20-5
2020-08-16 added code in camera to ESP32 transmit and code for receiver with packege count

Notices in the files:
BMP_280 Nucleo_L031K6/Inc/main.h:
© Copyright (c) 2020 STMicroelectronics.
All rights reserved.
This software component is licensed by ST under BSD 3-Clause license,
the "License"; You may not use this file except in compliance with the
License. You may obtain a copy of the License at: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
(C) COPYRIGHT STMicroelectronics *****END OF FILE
